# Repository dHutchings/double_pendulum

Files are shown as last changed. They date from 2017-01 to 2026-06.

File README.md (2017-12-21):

# double pendulum

A battery-powered low power double pendulum.  Useful for looking cool.  It's a good gift.

[Video of Final](https://youtu.be/Yj28coDq9EA)

[Video of Rev 3 Prototype](https://youtu.be/eYqc_CuFVBs)

[Video of Rev 2 Prototype](https://youtu.be/RyoI87ninAo)

[Video of Rev 1 Prototype](https://www.youtube.com/watch?v=9qNsIy8OKPE)

[Video of Proof of Concept](https://youtu.be/A4e-QBMb_Hc)

[Video of Back EMF Demo](https://youtu.be/CLvjtHWwjVc)

[BOM](https://docs.google.com/spreadsheets/d/1zQ9JefeK5bJ6EfoIBReY1vUxNtvPFnJwqca2jpHTiHs/edit#gid=1877369656)

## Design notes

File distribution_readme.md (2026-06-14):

## A List Showing the Distribution of Pendulums

#### Each Pendulum has a serial number, on a sticker, on the bottom of the base.

0. Douglas Hutchings  (Final prototype, brass is not polished)
1. Prof. Ronald Fearing (X)
2. Katherina Law (X) 
3. Prof. Oliver O'Reily (X)
4. Dr. George Anwar (X)
5. Jeremey Kramer (X)
6. Prof. Ruzena Bajcsy (X)
7. UC Berkeley MechE Machine Shop (X)
8. Dr. Eric Nelson (X)
9. Sold to Dr. Anwar (X)
10. Martin Kwitek (X)
11. Dr. Frank Ling (X)
12. Carl Page (X)
13. David Araujo ()

Intented:
14. Prof. Alice Agogino
15. Prof. Mark Mueller
16. Prof. Negar Mehr
17. UC Berkeley Hesse Hall Machine Shop
18. Dr. Deniz Dogruer
19. Dr. Alan Zhang
20. Katie Calvert
21. Kingston Chua
22. Ryan Ho.
23. Douglas Hutchings (rev E / D prototype)
24. Devin / Brian / Lee?  Tiffany / BG?

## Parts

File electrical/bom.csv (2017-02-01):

Name | Value | Package | Notes | Ref Number
C1 | 1000uF | CPOL-RADIAL-1000UF-25V | Capacitor Polarized
C2 | .1uF | 0603-CAP | Capacitor | CAPACITOR-GENERIC
C3 | 10uF | 0805 | Capacitor | CAPACITOR-GENERIC
C4 | .1uF | 0603-CAP | Capacitor | CAPACITOR-GENERIC
C5 | 10uF | 0805 | Capacitor | CAPACITOR-GENERIC
JP2 |  | 1X02 | 2-pin 0.1-inch header and MTA connector | BULK-STOCK
JP3 |  | 1X06 | PIN HEADER
Q1 | IRLIB9343PBF-ND | TO220 | P-Channel Enhancement MOSFET (HEXFET); -100V; -12A; 0,3Ohm
R1 | 10K | R0603 | RESISTOR, American symbol
R2 | 10K | R0603 | RESISTOR, American symbol
R3 | 10K | R0603 | RESISTOR, American symbol
R4 | 10K | R0603 | RESISTOR, American symbol
R5 | 10K | R0603 | RESISTOR, American symbol
R6 | 10K | R0603 | RESISTOR, American symbol
R7 | 10K | R0603 | RESISTOR, American symbol
R8 | 115k | R0603 | RESISTOR, American symbol
R9 | 10K | R0603 | RESISTOR, American symbol
S1 |  | TACTILE-PTH | Momentary Switch | pth_pushbutton
S2 |  | TACTILE-PTH | Momentary Switch | pth_pushbutton
S3 |  | TACTILE-PTH | Momentary Switch | pth_pushbutton
S4 |  | TACTILE-PTH | Momentary Switch | pth_pushbutton
ST1 | 2PIN_SCREW | 2PIN_SCREW | 2 Pin Screw Terminal
ST2 | 2PIN_SCREW | 2PIN_SCREW | 2 Pin Screw Terminal
S_PWR | SPDT_TOGGLE_SWITCH | E-SWITCH-SPDT | Toggle Switch SPDT Panel Mount
U1 | POLOLU_D24V22F5 | POLOLU_D24V22F5
U2 | TPS3710 | SOT6 | TI Low Voltage monitoring chip.
U3 | MCP4725 | SOT23-6 | Microchip 12-bit I2C DAC, SOT23-6
U4 | MCP4725 | SOT23-6 | Microchip 12-bit I2C DAC, SOT23-6
U5 | MCP6002 | DIL08 | Single Op Amp 2.7V to 6.0V Single Supply CMOS
UC1 | ARDUINO_PRO_MICRO | ARDUINO_PRO_MICRO | Arduino Pro Micro
USB1 | USB-OTGMICRO-AB | USB-MICRO-AB | USB Connector | USB

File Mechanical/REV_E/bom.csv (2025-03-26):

ITEM NO. | PART NUMBER | DESCRIPTION | QTY.
1 | 90633A005 |  | 6
2 | 92949A112 |  | 4
3 | Plate |  | 1
4 | 9541K8 |  | 4
5 | Base |  | 1
6 | Pillar |  | 1
7 | FR144-ZZ |  | 4
8 | 6433 |  | 1
9 | TATP-683-13 |  | 1
10 | RC22 |  | 1
11 | 94035A138 |  | 1
12 | bearing_spacer_ 99040A316 |  | 4
13 | 93286A005 |  | 11
14 | 92210A112 |  | 3
15 | Mass_blank |  | 1
16 | bottom_link |  | 1
17 | PCB_rev_a |  | 1
18 | bearing_offset |  | 1
19 | 94035A517 |  | 1
20 | 91780A167 |  | 2
21 | 93286A005 |  | 6
22 | 1155_battery_holder |  | 1
23 | 92141A009 |  | 2
24 | 93135A353 |  | 2
25 | 92949A113 |  | 2
26 | 92949A197 |  | 3
27 | top_link |  | 1

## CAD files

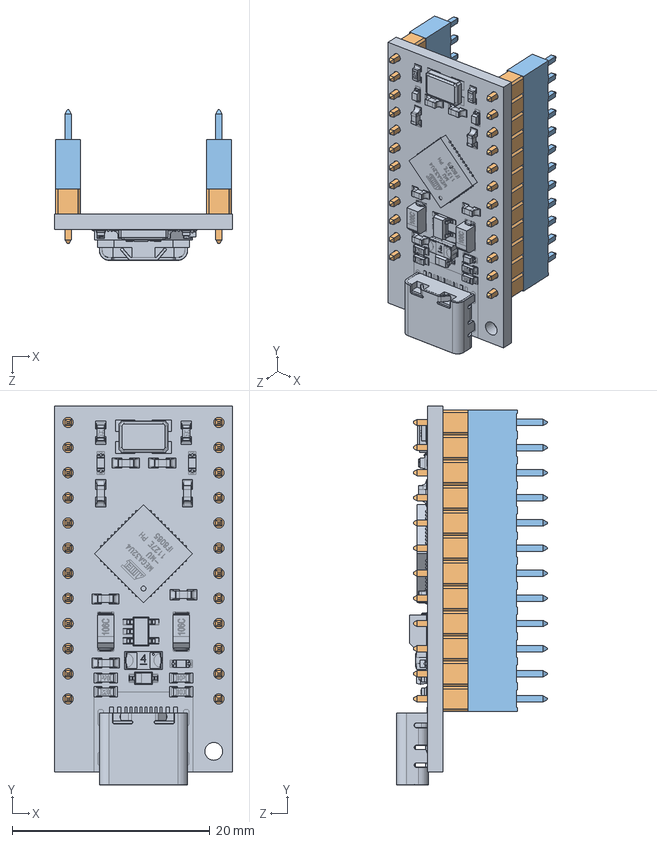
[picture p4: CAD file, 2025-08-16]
Mechanical/REV_E/pcb_parts/apm_usbc_removable.SLDASM
18.0 x 38.3 x 15.2 mm
ProMicroUSBC_Corrected
12pin_male_short x 2
12pin_female_short x 2

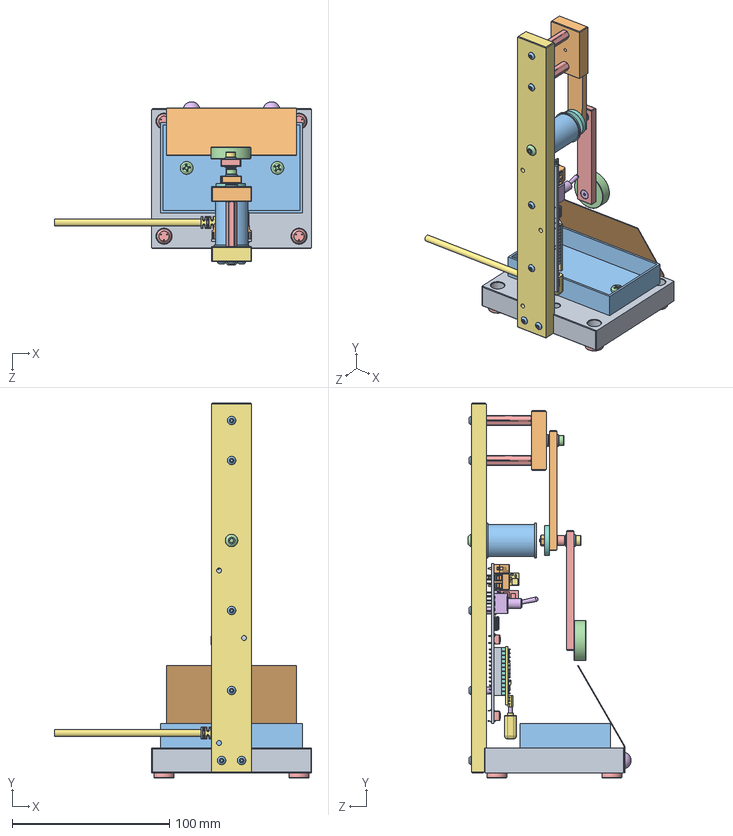
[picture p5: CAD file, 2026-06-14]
Mechanical/REV_E/Assem1.SLDASM
163.3 x 238.1 x 103.8 mm
Base
Plate
1155_battery_holder
8_32_500_nylon_93135A353 x 2
9309K62_Tight-Grip Push-In Bumpers x 4
90081A291_Zinc-Plated Steel Screw Nails x 2
Pillar
custom_spool x 2
Part4^electromagnet
8_32-750_stainless_92949A197
d45v1e1fx-step-down-voltage-regulators.step.step
Right angle pin header_03.step.step
step-up-voltage-regulator-u3v16fx.step.step
Right angle pin header_03.step (1).step
Board.step
2PIN_SCREW.step x 2
MCP6232.step x 2
0.033uF.step x 2
TACTILE-PTH.step x 4
SPDT_TOGGLE_SWITCH.step
STAND-OFFKEYSTONE_SMT_STANDOFF.step x 2
USB-C-16P-2LAYER-PADS.step
ICM7555.step
4.7uF.step x 2
600mA_40V.step
DMP3098.step
250mA_100V_350mV.step
220k.step x 3
220.step
CD40109B.step
LTC1661MSOP8.step
bearing_offset
4_40-625-Stainless-92949A811 x 6
4_40-625-countersunk-stainless-92210a112 x 2
4_40-1125-HEX Standoff_91780A629_Hex x 2
4_40_1-8_90176A102_Nylon Unthreaded Spacers x 2
ProMicroUSBC_Corrected
12pin_male_short x 2
12pin_female_short x 2
top_link
FR144-ZZ x 4
Mass_blank
bottom_link
92805A108_Stainless Steel Thread-Locking Hex Drive Flat Head Screws
4_40-3-4-94035A138
RC22
bearing_spacer_ 99040A316 x 4
4_40_THIN_LOCKNUT_90633A005
4_40-Washer_AL_93286A005
4_40-5-16_94035A517_new
1_8_3_16_92510A421_Aluminum Unthreaded Spacer-mod
Male USB C.step
USB C cord.step

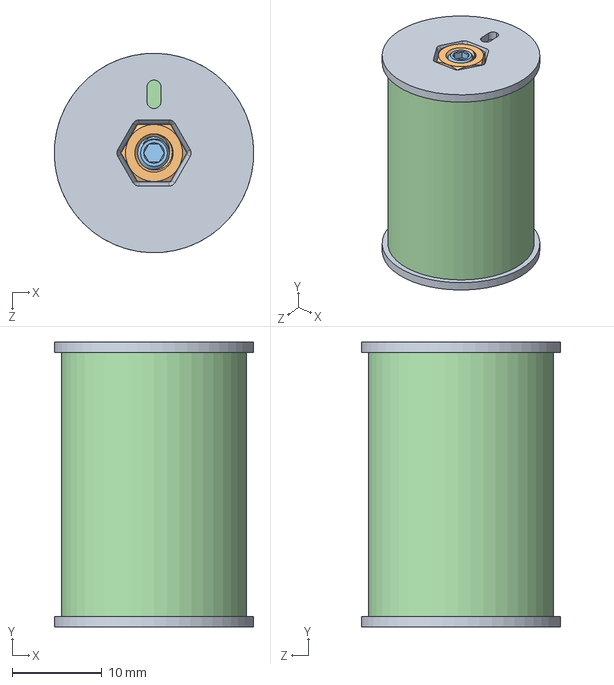
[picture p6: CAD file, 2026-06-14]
Mechanical/REV_E/electromagnet.SLDASM
22.2 x 31.8 x 22.2 mm
custom_spool x 2

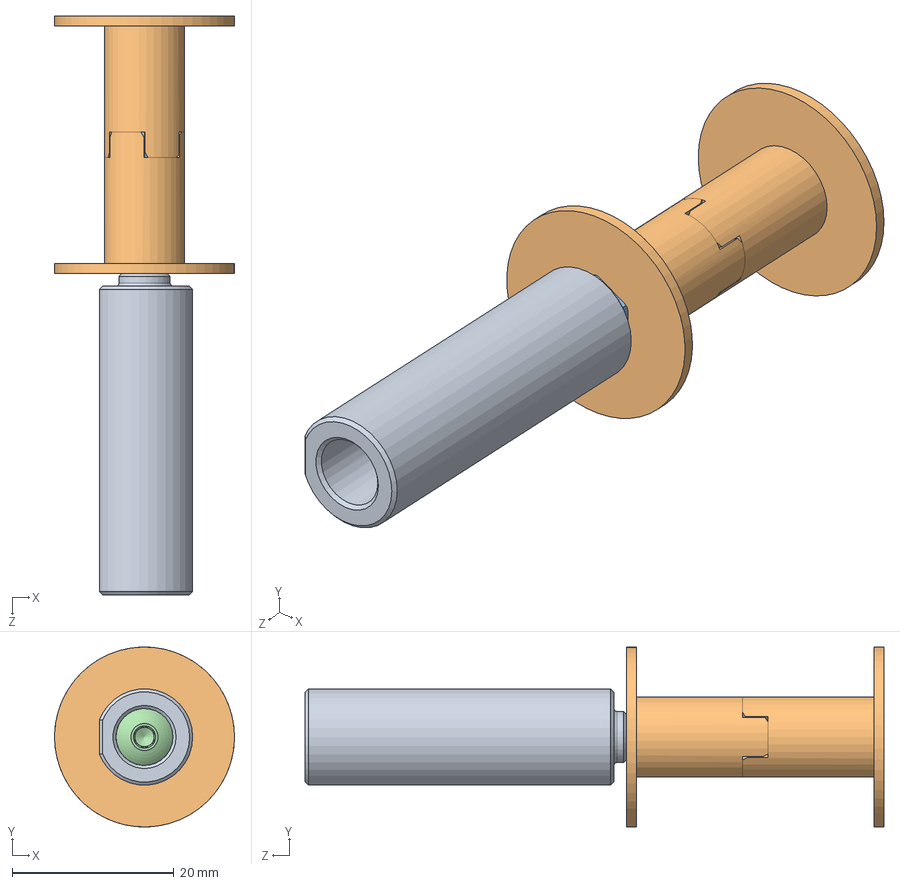
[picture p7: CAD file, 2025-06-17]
Mechanical/REV_E/tools/mandrel_assy.SLDASM
22.2 x 22.2 x 71.4 mm
winding_mandrel_machined
custom_spool x 2
91920A201_Female Threaded Hex Standoff
92949A197_18-8 Stainless Steel Button Head Hex Drive Screw

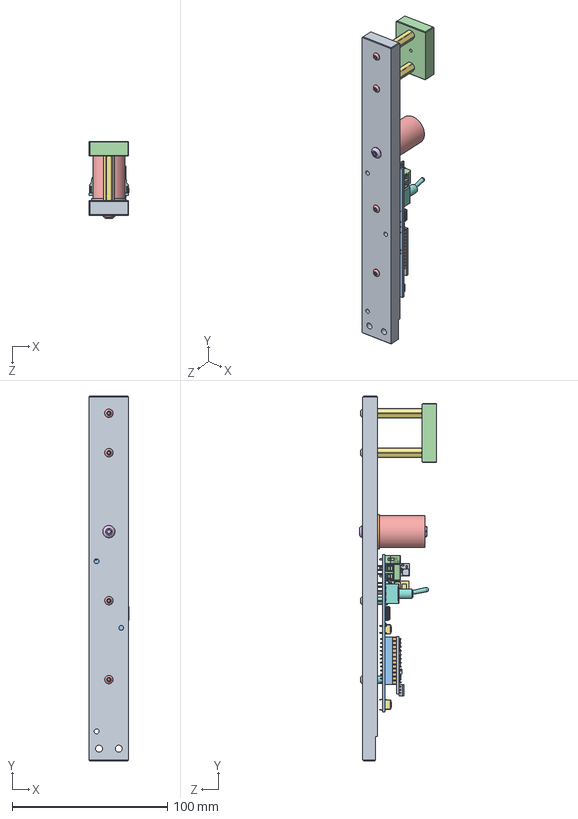
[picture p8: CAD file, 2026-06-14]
Mechanical/REV_E/Pillar_assy.sldasm
25.5 x 235.0 x 49.8 mm
Pillar
custom_spool
8_32-750_stainless_92949A197
d45v1e1fx-step-down-voltage-regulators.step.step
Right angle pin header_03.step.step
step-up-voltage-regulator-u3v16fx.step.step
Right angle pin header_03.step (1).step
Board.step
2PIN_SCREW.step x 2
MCP6232.step x 2
0.033uF.step x 2
TACTILE-PTH.step x 4
SPDT_TOGGLE_SWITCH.step
STAND-OFFKEYSTONE_SMT_STANDOFF.step x 2
USB-C-16P-2LAYER-PADS.step
ICM7555.step
4.7uF.step x 2
600mA_40V.step
DMP3098.step
250mA_100V_350mV.step
220k.step x 3
220.step
CD40109B.step
LTC1661MSOP8.step
bearing_offset
4_40-625-Stainless-92949A811 x 4
4_40-625-countersunk-stainless-92210a112 x 2
4_40-1125-HEX Standoff_91780A629_Hex x 2
4_40_1-8_90176A102_Nylon Unthreaded Spacers x 2
ProMicroUSBC_Corrected
12pin_male_short x 2
12pin_female_short x 2

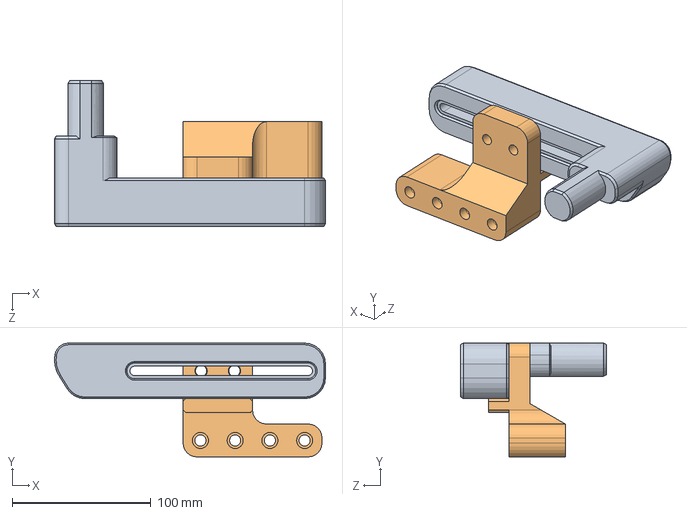
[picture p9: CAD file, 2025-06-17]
Mechanical/REV_E/tools/ShearStopAssy.SLDASM
195.0 x 81.9 x 105.0 mm
Press_brake_stop
ShearLowerArm

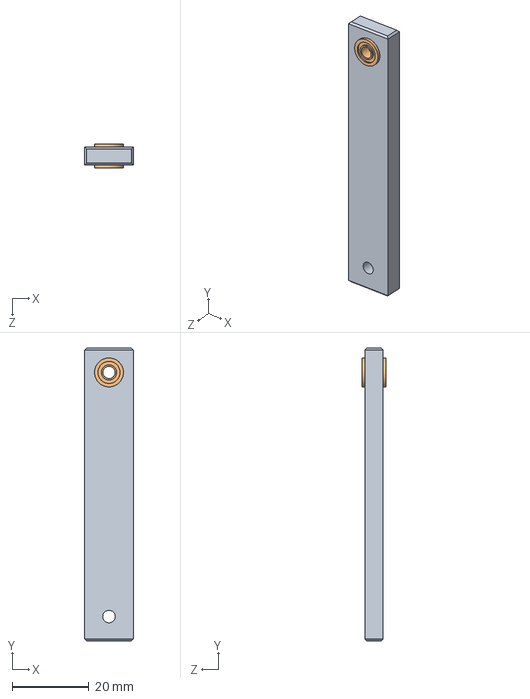
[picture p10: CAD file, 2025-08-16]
Mechanical/REV_E/top_link_assy.sldasm
12.7 x 76.2 x 6.34 mm
top_link
FR144-ZZ x 2

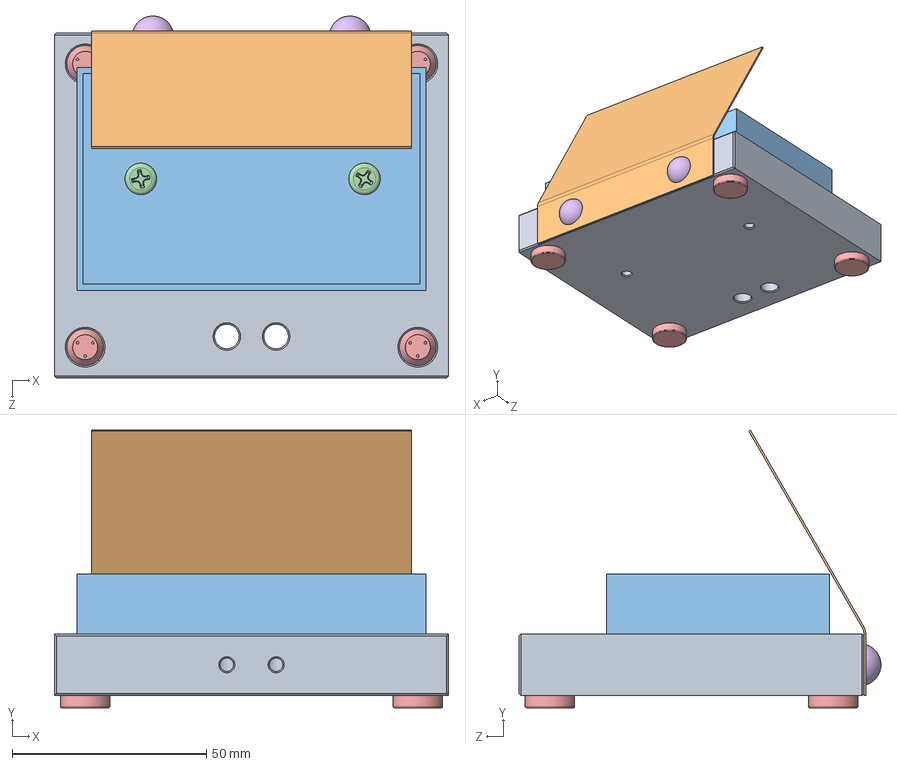
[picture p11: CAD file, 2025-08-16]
Mechanical/REV_E/Base_assy.sldasm
101.6 x 71.6 x 93.3 mm
Base
Plate
1155_battery_holder
8_32_500_nylon_93135A353 x 2
9309K62_Tight-Grip Push-In Bumpers x 4
90081A291_Zinc-Plated Steel Screw Nails x 2

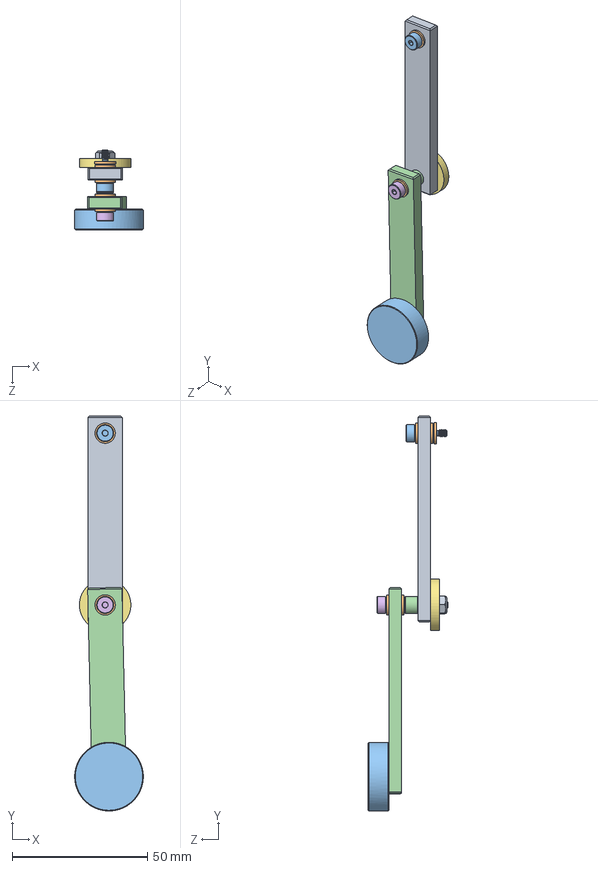
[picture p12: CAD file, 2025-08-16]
Mechanical/REV_E/pendulum.SLDASM
25.4 x 146.0 x 29.4 mm
top_link
FR144-ZZ x 4
Mass_blank
bottom_link
92805A108_Stainless Steel Thread-Locking Hex Drive Flat Head Screws
4_40-3-4-94035A138
RC22
bearing_spacer_ 99040A316 x 4
4_40_THIN_LOCKNUT_90633A005
4_40-Washer_AL_93286A005
4_40-5-16_94035A517_new
1_8_3_16_92510A421_Aluminum Unthreaded Spacer-mod

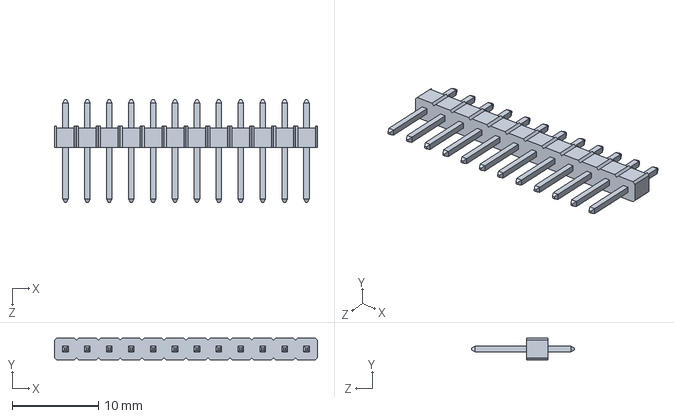
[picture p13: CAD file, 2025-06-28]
Mechanical/REV_E/pcb_parts/12pin_male.SLDASM
30.5 x 2.54 x 11.9 mm

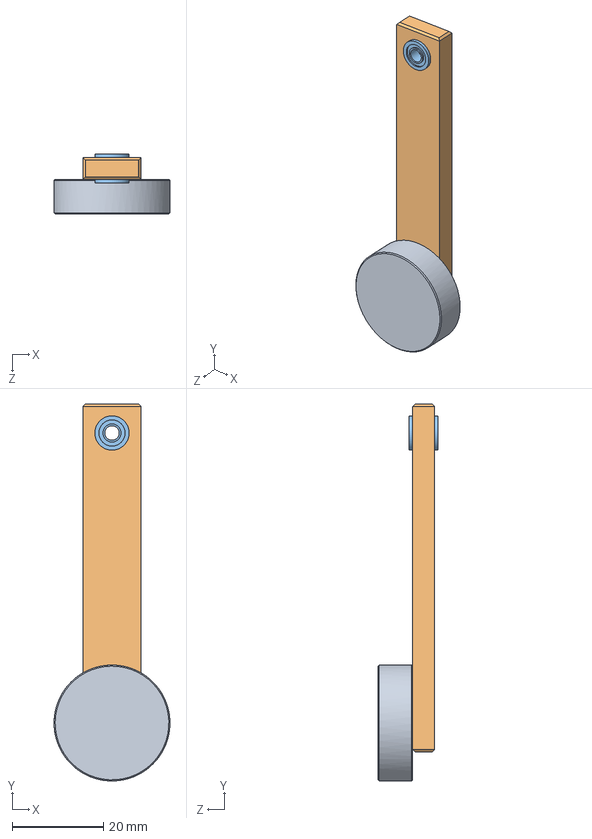
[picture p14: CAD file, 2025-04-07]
Mechanical/REV_E/bottom_link_assy.sldasm
25.4 x 82.5 x 13.2 mm
Mass_blank
bottom_link
FR144-ZZ x 2
92805A108_Stainless Steel Thread-Locking Hex Drive Flat Head Screws

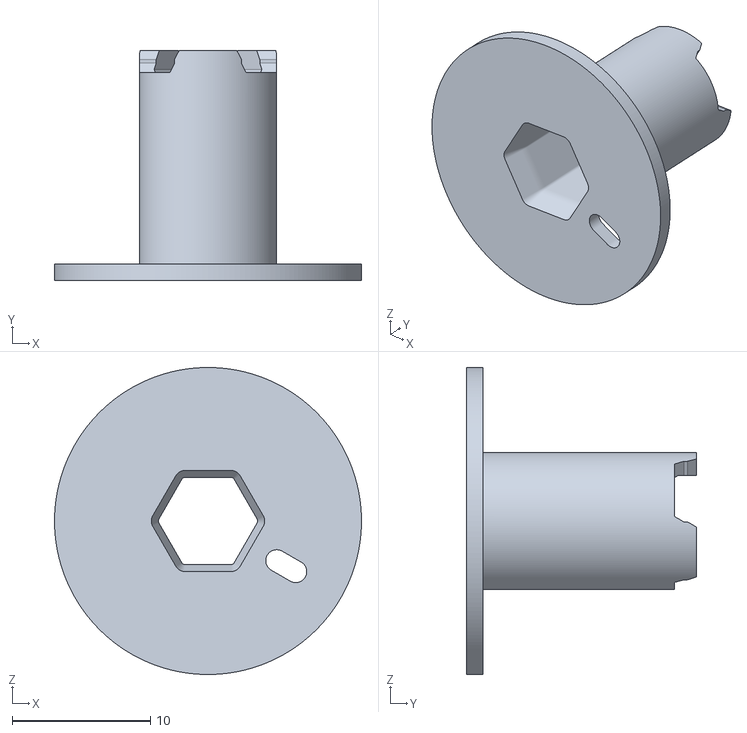
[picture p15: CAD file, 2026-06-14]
Mechanical/REV_E/printables/custom_spool_xometry_pressfit.STL
22.2 x 16.7 x 22.2

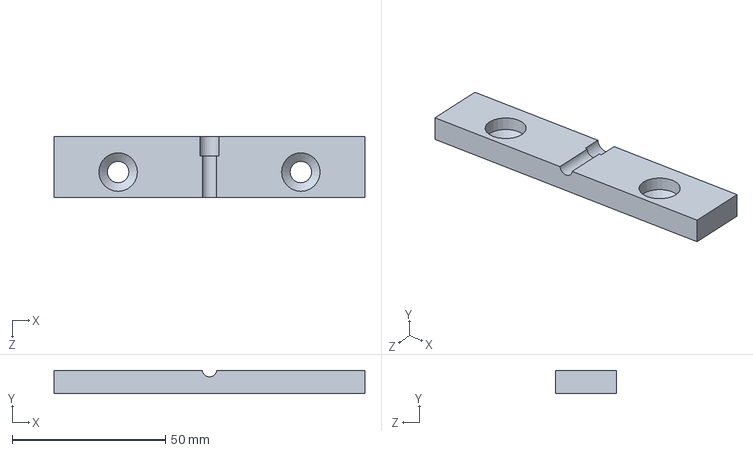
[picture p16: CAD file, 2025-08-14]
Mechanical/REV_E/tools/clamp.SLDPRT
101.6 x 7.62 x 19.8 mm

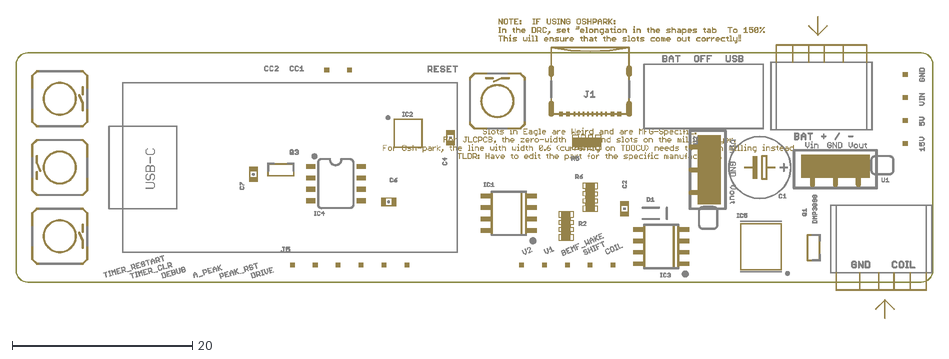
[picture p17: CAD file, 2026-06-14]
Mechanical/REV_E/controller_revD5.dxf
101.6 x 33.5

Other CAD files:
Mechanical/REV_E/controller_d5_san.DXF
Mechanical/REV_E/pcb_parts/Right angle pin header_03.STEP
Mechanical/REV_E/printables/custom_spool_xometry_clearance.STL
Mechanical/REV_E/tools/winding_mandrel_machined.SLDPRT
Mechanical/REV_C/4-40-75-92949A113_.SLDPRT
Mechanical/REV_C/4-40-750-Nylon_93135A278.SLDPRT
Mechanical/REV_C/4-40_15-32_5-32_94035A134.SLDPRT
Mechanical/REV_C/4-40_7-16_5-32_94035A521.SLDPRT
Mechanical/REV_C/4_40-125_spacer_nylon_94639A199.SLDPRT
Mechanical/REV_C/4_40-50-91255A110.SLDPRT
Mechanical/REV_C/4_40-50-92949A110.SLDPRT
Mechanical/REV_C/4_40-562-Stainless-92949A112.SLDPRT
Mechanical/REV_C/4_40-625-countersunk-91253A112.SLDPRT
Mechanical/REV_C/4_40-75-91255A113.SLDPRT
Mechanical/REV_C/4_40-Washer_AL_93286A005.SLDPRT
Mechanical/REV_C/4_40_1750-HEX STANDOFF91780A038.SLDPRT
Mechanical/REV_C/8_32-625-97763A333.SLDPRT
Mechanical/REV_C/8_32-750-91255A197-new.SLDPRT
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

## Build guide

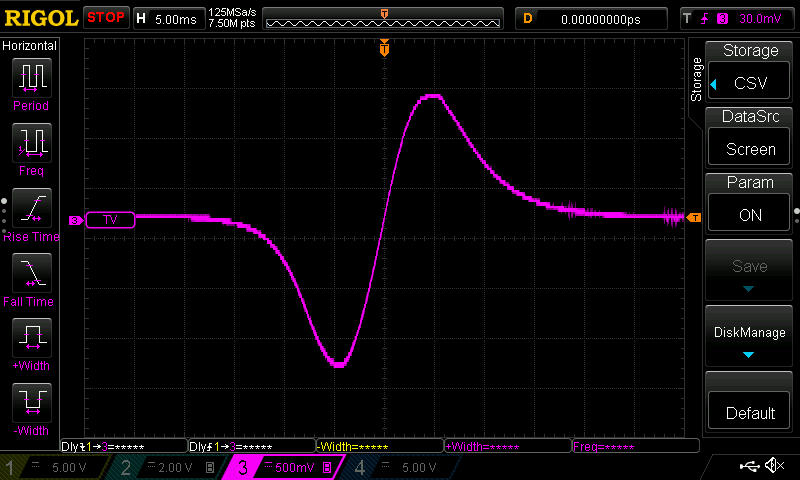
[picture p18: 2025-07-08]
electrical/back_emf/DS1Z_QuickPrint5_ragged.jpg

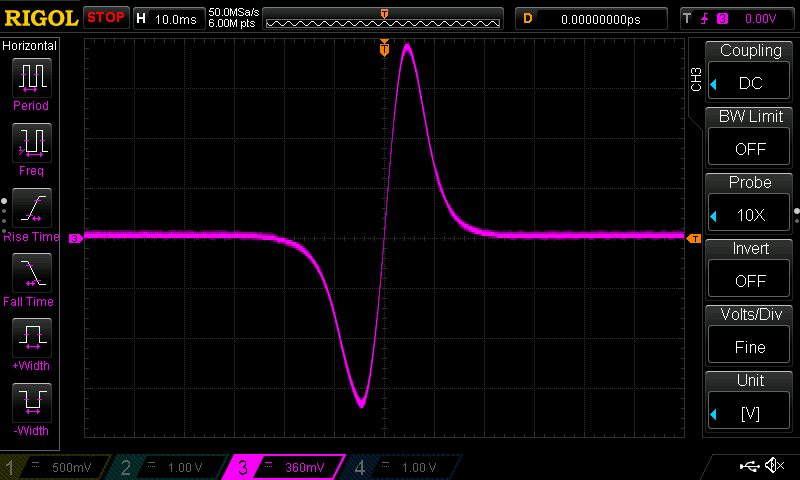
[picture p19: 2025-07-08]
electrical/back_emf/DS1Z_QuickPrint1_clean.png

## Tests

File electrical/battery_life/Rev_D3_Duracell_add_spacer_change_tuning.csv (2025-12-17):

FLUKE 289 | V1.16 | 40810170 Douglas Hutchings
To display full timestamps use Format Cells ‘m/d/y hh:mm:ss.0'
Start Time | Stop Time | Elapsed Time | Interval | Total readings | Intervals | Input Events | Session Name
12/14/2025 6:20:07 PM | 12/16/2025 11:44:42 AM | 41:24:35 | 0:01:00 | 11096 | 2485 | 8786 | Motor 11
Max Time | Max | Average | Min | Min Time | Scaling
12/14/2025 6:20:07 PM | 10.130 V DC | 6.737 V DC | 1.3092 V DC | 12/16/2025 12:12:04 AM | (none)
Reading | Sample | Start Time | Duration | Max Time | Max | Average | Min Time | Min | Description | Stop Time
1 | 10.130 V DC | 12/14/2025 18:20:07.3 | 0:00:03.2 | 12/14/2025 18:20:07.3 | 10.130 V DC | 10.108 V DC | 12/14/2025 18:20:10.1 | 10.033 V DC | Stable | 12/14/2025 18:20:10.5
2 | 9.406 V DC | 12/14/2025 18:20:10.5 | 0:00:03.2 | 12/14/2025 18:20:11.2 | 9.943 V DC | 9.084 V DC | 12/14/2025 18:20:13.1 | 8.402 V DC | Unstable | 12/14/2025 18:20:13.7
3 | 9.884 V DC | 12/14/2025 18:20:13.7 | 0:00:01.9 | 12/14/2025 18:20:15.6 | 9.987 V DC | 9.948 V DC | 12/14/2025 18:20:13.7 | 9.884 V DC | Stable | 12/14/2025 18:20:15.7
4 | 9.990 V DC | 12/14/2025 18:20:15.7 | 0:00:04.6 | 12/14/2025 18:20:16.1 | 10.000 V DC | 9.266 V DC | 12/14/2025 18:20:19.1 | 8.384 V DC | Unstable | 12/14/2025 18:20:20.3
5 | 9.859 V DC | 12/14/2025 18:20:20.3 | 0:00:06.8 | 12/14/2025 18:20:23.7 | 9.960 V DC | 9.908 V DC | 12/14/2025 18:20:20.5 | 9.799 V DC | Stable | 12/14/2025 18:20:27.1
6 | 9.977 V DC | 12/14/2025 18:20:27.1 | 0:00:00.1 | 12/14/2025 18:20:27.1 | 9.977 V DC | 9.977 V DC | 12/14/2025 18:20:27.1 | 9.977 V DC | Unstable | 12/14/2025 18:20:27.2
7 | 9.868 V DC | 12/14/2025 18:20:27.2 | 0:00:02.8 | 12/14/2025 18:20:29.8 | 10.005 V DC | 9.980 V DC | 12/14/2025 18:20:27.2 | 9.868 V DC | Stable | 12/14/2025 18:20:30.0
8 | 10.006 V DC | 12/14/2025 18:20:30.0 | 0:00:03.1 | 12/14/2025 18:20:32.5 | 10.018 V DC | 9.995 V DC | 12/14/2025 18:20:32.9 | 9.957 V DC | Stable | 12/14/2025 18:20:33.2
9 | 9.876 V DC | 12/14/2025 18:20:33.2 | 0:00:00.3 | 12/14/2025 18:20:33.4 | 9.993 V DC | 9.939 V DC | 12/14/2025 18:20:33.2 | 9.876 V DC | Unstable | 12/14/2025 18:20:33.5
10 | 10.012 V DC | 12/14/2025 18:20:33.5 | 0:00:33.3 | 12/14/2025 18:21:04.4 | 10.055 V DC | 10.024 V DC | 12/14/2025 18:21:00.6 | 9.923 V DC | Interval | 12/14/2025 18:21:06.8
11 | 9.996 V DC | 12/14/2025 18:21:06.8 | 0:00:37.1 | 12/14/2025 18:21:42.3 | 10.066 V DC | 10.044 V DC | 12/14/2025 18:21:21.8 | 9.934 V DC | Stable | 12/14/2025 18:21:43.9
12 | 9.917 V DC | 12/14/2025 18:21:43.9 | 0:00:00.1 | 12/14/2025 18:21:43.9 | 9.917 V DC | 9.917 V DC | 12/14/2025 18:21:43.9 | 9.917 V DC | Unstable | 12/14/2025 18:21:44.0
13 | 10.036 V DC | 12/14/2025 18:21:44.0 | 0:00:14.8 | 12/14/2025 18:21:52.2 | 10.063 V DC | 10.041 V DC | 12/14/2025 18:21:46.3 | 9.965 V DC | Stable | 12/14/2025 18:21:58.8
14 | 9.911 V DC | 12/14/2025 18:21:58.8 | 0:00:00.1 | 12/14/2025 18:21:58.8 | 9.911 V DC | 9.911 V DC | 12/14/2025 18:21:58.8 | 9.911 V DC | Unstable | 12/14/2025 18:21:58.9
15 | 10.039 V DC | 12/14/2025 18:21:58.9 | 0:00:07.8 | 12/14/2025 18:22:01.4 | 10.063 V DC | 10.045 V DC | 12/14/2025 18:22:00.7 | 9.988 V DC | Interval | 12/14/2025 18:22:06.7
16 | 10.064 V DC | 12/14/2025 18:22:06.7 | 0:00:17.2 | 12/14/2025 18:22:17.7 | 10.065 V DC | 10.043 V DC | 12/14/2025 18:22:19.6 | 9.942 V DC | Stable | 12/14/2025 18:22:23.9
17 | 9.870 V DC | 12/14/2025 18:22:23.9 | 0:00:00.1 | 12/14/2025 18:22:23.9 | 9.870 V DC | 9.870 V DC | 12/14/2025 18:22:23.9 | 9.870 V DC | Unstable | 12/14/2025 18:22:24.0
18 | 10.025 V DC | 12/14/2025 18:22:24.0 | 0:00:03.9 | 12/14/2025 18:22:27.9 | 10.063 V DC | 10.042 V DC | 12/14/2025 18:22:26.8 | 9.969 V DC | Stable | 12/14/2025 18:22:28.0
19 | 9.927 V DC | 12/14/2025 18:22:28.0 | 0:00:00.2 | 12/14/2025 18:22:28.1 | 9.961 V DC | 9.944 V DC | 12/14/2025 18:22:28.0 | 9.927 V DC | Unstable | 12/14/2025 18:22:28.2
20 | 10.046 V DC | 12/14/2025 18:22:28.2 | 0:00:25.1 | 12/14/2025 18:22:49.5 | 10.065 V DC | 10.043 V DC | 12/14/2025 18:22:35.2 | 9.957 V DC | Stable | 12/14/2025 18:22:53.3
21 | 9.938 V DC | 12/14/2025 18:22:53.3 | 0:00:00.1 | 12/14/2025 18:22:53.3 | 9.938 V DC | 9.938 V DC | 12/14/2025 18:22:53.3 | 9.938 V DC | Unstable | 12/14/2025 18:22:53.4
22 | 10.047 V DC | 12/14/2025 18:22:53.4 | 0:00:01.1 | 12/14/2025 18:22:54.4 | 10.062 V DC | 10.049 V DC | 12/14/2025 18:22:53.6 | 10.021 V DC | Stable | 12/14/2025 18:22:54.5
23 | 9.938 V DC | 12/14/2025 18:22:54.5 | 0:00:00.4 | 12/14/2025 18:22:54.8 | 10.040 V DC | 9.972 V DC | 12/14/2025 18:22:54.5 | 9.938 V DC | Unstable | 12/14/2025 18:22:54.9
24 | 10.056 V DC | 12/14/2025 18:22:54.9 | 0:00:11.9 | 12/14/2025 18:23:04.3 | 10.063 V DC | 10.039 V DC | 12/14/2025 18:22:57.9 | 9.946 V DC | Interval | 12/14/2025 18:23:06.8
25 | 10.061 V DC | 12/14/2025 18:23:06.8 | 0:00:07.3 | 12/14/2025 18:23:11.3 | 10.063 V DC | 10.043 V DC | 12/14/2025 18:23:06.9 | 9.981 V DC | Stable | 12/14/2025 18:23:14.1
26 | 9.904 V DC | 12/14/2025 18:23:14.1 | 0:00:00.1 | 12/14/2025 18:23:14.1 | 9.904 V DC | 9.904 V DC | 12/14/2025 18:23:14.1 | 9.904 V DC | Unstable | 12/14/2025 18:23:14.3
27 | 10.041 V DC | 12/14/2025 18:23:14.3 | 0:00:41.5 | 12/14/2025 18:23:23.8 | 10.063 V DC | 10.043 V DC | 12/14/2025 18:23:32.1 | 9.943 V DC | Stable | 12/14/2025 18:23:55.8
28 | 9.930 V DC | 12/14/2025 18:23:55.8 | 0:00:11.0 | 12/14/2025 18:23:59.7 | 10.061 V DC | 10.032 V DC | 12/14/2025 18:24:05.5 | 9.915 V DC | Interval | 12/14/2025 18:24:06.8
29 | 10.058 V DC | 12/14/2025 18:24:06.8 | 0:00:01.2 | 12/14/2025 18:24:06.8 | 10.058 V DC | 10.033 V DC | 12/14/2025 18:24:07.7 | 9.935 V DC | Unstable | 12/14/2025 18:24:08.0
30 | 10.055 V DC | 12/14/2025 18:24:08.0 | 0:00:58.8 | 12/14/2025 18:24:26.5 | 10.060 V DC | 10.037 V DC | 12/14/2025 18:24:32.0 | 9.925 V DC | Interval | 12/14/2025 18:25:06.7
31 | 10.058 V DC | 12/14/2025 18:25:06.7 | 0:00:02.7 | 12/14/2025 18:25:06.8 | 10.059 V DC | 10.045 V DC | 12/14/2025 18:25:08.4 | 9.986 V DC | Stable | 12/14/2025 18:25:09.4
32 | 9.939 V DC | 12/14/2025 18:25:09.4 | 0:00:57.3 | 12/14/2025 18:25:22.8 | 10.057 V DC | 10.033 V DC | 12/14/2025 18:25:15.5 | 9.889 V DC | Interval | 12/14/2025 18:26:06.8
33 | 10.052 V DC | 12/14/2025 18:26:06.8 | 0:00:12.7 | 12/14/2025 18:26:08.2 | 10.055 V DC | 10.032 V DC | 12/14/2025 18:26:10.2 | 9.953 V DC | Stable | 12/14/2025 18:26:19.5
34 | 9.934 V DC | 12/14/2025 18:26:19.5 | 0:00:00.1 | 12/14/2025 18:26:19.5 | 9.934 V DC | 9.934 V DC | 12/14/2025 18:26:19.5 | 9.934 V DC | Unstable | 12/14/2025 18:26:19.6
35 | 10.036 V DC | 12/14/2025 18:26:19.6 | 0:00:06.5 | 12/14/2025 18:26:23.1 | 10.052 V DC | 10.027 V DC | 12/14/2025 18:26:20.4 | 9.934 V DC | Stable | 12/14/2025 18:26:26.1
36 | 9.915 V DC | 12/14/2025 18:26:26.1 | 0:00:40.6 | 12/14/2025 18:26:29.2 | 10.051 V DC | 10.025 V DC | 12/14/2025 18:26:42.8 | 9.857 V DC | Interval | 12/14/2025 18:27:06.8
37 | 10.048 V DC | 12/14/2025 18:27:06.8 | 0:00:17.4 | 12/14/2025 18:27:07.6 | 10.049 V DC | 10.028 V DC | 12/14/2025 18:27:07.7 | 9.946 V DC | Stable | 12/14/2025 18:27:24.2
38 | 9.896 V DC | 12/14/2025 18:27:24.2 | 0:00:07.5 | 12/14/2025 18:27:26.5 | 10.044 V DC | 10.011 V DC | 12/14/2025 18:27:28.2 | 9.894 V DC | Stable | 12/14/2025 18:27:31.7
39 | 10.045 V DC | 12/14/2025 18:27:31.7 | 0:00:23.9 | 12/14/2025 18:27:48.6 | 10.047 V DC | 10.022 V DC | 12/14/2025 18:27:34.8 | 9.922 V DC | Stable | 12/14/2025 18:27:55.7
40 | 9.877 V DC | 12/14/2025 18:27:55.7 | 0:00:00.1 | 12/14/2025 18:27:55.7 | 9.877 V DC | 9.877 V DC | 12/14/2025 18:27:55.7 | 9.877 V DC | Unstable | 12/14/2025 18:27:55.8
41 | 9.996 V DC | 12/14/2025 18:27:55.8 | 0:00:11.1 | 12/14/2025 18:28:04.0 | 10.041 V DC | 10.002 V DC | 12/14/2025 18:27:57.2 | 9.886 V DC | Interval | 12/14/2025 18:28:06.8
42 | 9.987 V DC | 12/14/2025 18:28:06.8 | 0:00:10.4 | 12/14/2025 18:28:12.6 | 10.042 V DC | 10.019 V DC | 12/14/2025 18:28:12.8 | 9.926 V DC | Stable | 12/14/2025 18:28:17.2
43 | 9.888 V DC | 12/14/2025 18:28:17.2 | 0:00:00.1 | 12/14/2025 18:28:17.2 | 9.888 V DC | 9.888 V DC | 12/14/2025 18:28:17.2 | 9.888 V DC | Unstable | 12/14/2025 18:28:17.3
44 | 10.017 V DC | 12/14/2025 18:28:17.3 | 0:00:13.7 | 12/14/2025 18:28:20.6 | 10.041 V DC | 10.021 V DC | 12/14/2025 18:28:27.9 | 9.942 V DC | Stable | 12/14/2025 18:28:31.0
45 | 9.924 V DC | 12/14/2025 18:28:31.0 | 0:00:35.8 | 12/14/2025 18:28:33.9 | 10.043 V DC | 10.017 V DC | 12/14/2025 18:28:57.4 | 9.880 V DC | Interval | 12/14/2025 18:29:06.8
46 | 10.036 V DC | 12/14/2025 18:29:06.8 | 0:00:02.9 | 12/14/2025 18:29:07.6 | 10.040 V DC | 10.024 V DC | 12/14/2025 18:29:08.9 | 9.961 V DC | Stable | 12/14/2025 18:29:09.7
47 | 9.915 V DC | 12/14/2025 18:29:09.7 | 0:00:00.1 | 12/14/2025 18:29:09.7 | 9.915 V DC | 9.915 V DC | 12/14/2025 18:29:09.7 | 9.915 V DC | Unstable | 12/14/2025 18:29:09.8
48 | 10.020 V DC | 12/14/2025 18:29:09.8 | 0:00:15.5 | 12/14/2025 18:29:14.4 | 10.040 V DC | 10.014 V DC | 12/14/2025 18:29:15.1 | 9.929 V DC | Stable | 12/14/2025 18:29:25.3
49 | 9.925 V DC | 12/14/2025 18:29:25.3 | 0:00:41.4 | 12/14/2025 18:30:00.3 | 10.038 V DC | 10.014 V DC | 12/14/2025 18:29:25.6 | 9.880 V DC | Interval | 12/14/2025 18:30:06.7
50 | 10.029 V DC | 12/14/2025 18:30:06.7 | 0:00:09.1 | 12/14/2025 18:30:10.5 | 10.037 V DC | 10.017 V DC | 12/14/2025 18:30:07.0 | 9.939 V DC | Stable | 12/14/2025 18:30:15.8
51 | 9.929 V DC | 12/14/2025 18:30:15.8 | 0:00:51.0 | 12/14/2025 18:30:21.6 | 10.036 V DC | 10.012 V DC | 12/14/2025 18:30:56.8 | 9.881 V DC | Interval | 12/14/2025 18:31:06.8
52 | 10.028 V DC | 12/14/2025 18:31:06.8 | 0:00:26.3 | 12/14/2025 18:31:16.7 | 10.034 V DC | 10.010 V DC | 12/14/2025 18:31:29.5 | 9.919 V DC | Stable | 12/14/2025 18:31:33.1
53 | 9.897 V DC | 12/14/2025 18:31:33.1 | 0:00:33.7 | 12/14/2025 18:31:46.3 | 10.029 V DC | 10.000 V DC | 12/14/2025 18:31:33.1 | 9.897 V DC | Interval | 12/14/2025 18:32:06.8
54 | 10.025 V DC | 12/14/2025 18:32:06.8 | 0:00:16.2 | 12/14/2025 18:32:11.7 | 10.028 V DC | 10.004 V DC | 12/14/2025 18:32:22.8 | 9.931 V DC | Stable | 12/14/2025 18:32:23.0
55 | 9.916 V DC | 12/14/2025 18:32:23.0 | 0:00:44.1 | 12/14/2025 18:32:30.5 | 10.027 V DC | 9.998 V DC | 12/14/2025 18:32:32.8 | 9.871 V DC | Interval | 12/14/2025 18:33:07.0
56 | 10.021 V DC | 12/14/2025 18:33:07.0 | 0:00:31.6 | 12/14/2025 18:33:31.6 | 10.023 V DC | 9.999 V DC | 12/14/2025 18:33:12.3 | 9.909 V DC | Stable | 12/14/2025 18:33:38.6
57 | 9.869 V DC | 12/14/2025 18:33:38.6 | 0:00:00.1 | 12/14/2025 18:33:38.6 | 9.869 V DC | 9.869 V DC | 12/14/2025 18:33:38.6 | 9.869 V DC | Unstable | 12/14/2025 18:33:38.7
58 | 9.995 V DC | 12/14/2025 18:33:38.7 | 0:00:16.9 | 12/14/2025 18:33:44.8 | 10.021 V DC | 10.002 V DC | 12/14/2025 18:33:51.5 | 9.934 V DC | Stable | 12/14/2025 18:33:55.6
59 | 9.841 V DC | 12/14/2025 18:33:55.6 | 0:00:00.1 | 12/14/2025 18:33:55.6 | 9.841 V DC | 9.841 V DC | 12/14/2025 18:33:55.6 | 9.841 V DC | Unstable | 12/14/2025 18:33:55.7
60 | 9.989 V DC | 12/14/2025 18:33:55.7 | 0:00:11.1 | 12/14/2025 18:34:01.4 | 10.020 V DC | 9.999 V DC | 12/14/2025 18:33:55.9 | 9.926 V DC | Interval | 12/14/2025 18:34:06.8
61 | 10.005 V DC | 12/14/2025 18:34:06.8 | 0:00:06.1 | 12/14/2025 18:34:08.4 | 10.021 V DC | 9.998 V DC | 12/14/2025 18:34:12.3 | 9.924 V DC | Stable | 12/14/2025 18:34:12.9
62 | 9.886 V DC | 12/14/2025 18:34:12.9 | 0:00:00.1 | 12/14/2025 18:34:12.9 | 9.886 V DC | 9.886 V DC | 12/14/2025 18:34:12.9 | 9.886 V DC | Unstable | 12/14/2025 18:34:13.0
63 | 9.996 V DC | 12/14/2025 18:34:13.0 | 0:00:25.5 | 12/14/2025 18:34:24.4 | 10.020 V DC | 9.998 V DC | 12/14/2025 18:34:30.4 | 9.909 V DC | Stable | 12/14/2025 18:34:38.5
64 | 9.893 V DC | 12/14/2025 18:34:38.5 | 0:00:28.3 | 12/14/2025 18:34:45.3 | 10.019 V DC | 9.996 V DC | 12/14/2025 18:34:38.5 | 9.893 V DC | Interval | 12/14/2025 18:35:06.7
65 | 10.013 V DC | 12/14/2025 18:35:06.7 | 0:00:06.7 | 12/14/2025 18:35:09.1 | 10.017 V DC | 9.999 V DC | 12/14/2025 18:35:09.2 | 9.938 V DC | Stable | 12/14/2025 18:35:13.5
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

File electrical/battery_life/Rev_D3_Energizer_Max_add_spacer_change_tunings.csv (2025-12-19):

FLUKE 289 | V1.16 | 40810170 Douglas Hutchings
To display full timestamps use Format Cells ‘m/d/y hh:mm:ss.0'
Start Time | Stop Time | Elapsed Time | Interval | Total readings | Intervals | Input Events | Session Name
12/16/2025 12:10:30 PM | 12/17/2025 1:19:52 PM | 25:09:23 | 0:01:00 | 10121 | 1510 | 8783 | Motor 12
Max Time | Max | Average | Min | Min Time | Scaling
12/16/2025 12:10:30 PM | 9.695 V DC | 7.577 V DC | 1.336 V DC | 12/17/2025 9:58:43 AM | (none)
Reading | Sample | Start Time | Duration | Max Time | Max | Average | Min Time | Min | Description | Stop Time
1 | 9.695 V DC | 12/16/2025 12:10:29.9 | 0:00:05.3 | 12/16/2025 12:10:29.9 | 9.695 V DC | 8.931 V DC | 12/16/2025 12:10:31.8 | 7.747 V DC | Unstable | 12/16/2025 12:10:35.2
2 | 9.512 V DC | 12/16/2025 12:10:35.2 | 0:00:05.4 | 12/16/2025 12:10:40.5 | 9.612 V DC | 9.564 V DC | 12/16/2025 12:10:35.6 | 9.476 V DC | Stable | 12/16/2025 12:10:40.6
3 | 9.614 V DC | 12/16/2025 12:10:40.6 | 0:00:03.4 | 12/16/2025 12:10:43.9 | 9.628 V DC | 9.605 V DC | 12/16/2025 12:10:41.9 | 9.535 V DC | Stable | 12/16/2025 12:10:44.0
4 | 9.480 V DC | 12/16/2025 12:10:44.0 | 0:00:00.4 | 12/16/2025 12:10:44.3 | 9.613 V DC | 9.555 V DC | 12/16/2025 12:10:44.0 | 9.480 V DC | Unstable | 12/16/2025 12:10:44.4
5 | 9.625 V DC | 12/16/2025 12:10:44.4 | 0:00:44.8 | 12/16/2025 12:11:29.0 | 9.657 V DC | 9.628 V DC | 12/16/2025 12:11:16.9 | 9.507 V DC | Interval | 12/16/2025 12:11:29.2
6 | 9.628 V DC | 12/16/2025 12:11:29.2 | 0:00:18.7 | 12/16/2025 12:11:47.2 | 9.660 V DC | 9.637 V DC | 12/16/2025 12:11:42.9 | 9.548 V DC | Stable | 12/16/2025 12:11:47.9
7 | 8.747 V DC | 12/16/2025 12:11:47.9 | 0:00:03.4 | 12/16/2025 12:11:48.5 | 9.499 V DC | 8.619 V DC | 12/16/2025 12:11:50.5 | 7.804 V DC | Unstable | 12/16/2025 12:11:51.4
8 | 9.480 V DC | 12/16/2025 12:11:51.4 | 0:00:04.4 | 12/16/2025 12:11:55.1 | 9.572 V DC | 9.529 V DC | 12/16/2025 12:11:53.1 | 9.469 V DC | Stable | 12/16/2025 12:11:55.8
9 | 9.578 V DC | 12/16/2025 12:11:55.8 | 0:00:14.7 | 12/16/2025 12:12:09.9 | 9.624 V DC | 9.594 V DC | 12/16/2025 12:11:59.2 | 9.526 V DC | Stable | 12/16/2025 12:12:10.5
10 | 8.096 V DC | 12/16/2025 12:12:10.5 | 0:00:03.5 | 12/16/2025 12:12:11.1 | 9.492 V DC | 8.666 V DC | 12/16/2025 12:12:13.0 | 7.820 V DC | Unstable | 12/16/2025 12:12:14.0
11 | 9.464 V DC | 12/16/2025 12:12:14.0 | 0:00:07.0 | 12/16/2025 12:12:20.1 | 9.560 V DC | 9.513 V DC | 12/16/2025 12:12:14.2 | 9.414 V DC | Stable | 12/16/2025 12:12:21.0
12 | 9.564 V DC | 12/16/2025 12:12:21.0 | 0:00:08.2 | 12/16/2025 12:12:28.7 | 9.586 V DC | 9.558 V DC | 12/16/2025 12:12:24.1 | 9.467 V DC | Interval | 12/16/2025 12:12:29.2
13 | 9.534 V DC | 12/16/2025 12:12:29.2 | 0:01:00.1 | 12/16/2025 12:13:25.3 | 9.621 V DC | 9.591 V DC | 12/16/2025 12:12:33.0 | 9.488 V DC | Interval | 12/16/2025 12:13:29.2
14 | 9.575 V DC | 12/16/2025 12:13:29.2 | 0:00:44.2 | 12/16/2025 12:14:12.7 | 9.629 V DC | 9.607 V DC | 12/16/2025 12:13:33.0 | 9.505 V DC | Stable | 12/16/2025 12:14:13.4
15 | 9.468 V DC | 12/16/2025 12:14:13.4 | 0:00:03.8 | 12/16/2025 12:14:14.1 | 9.495 V DC | 8.812 V DC | 12/16/2025 12:14:15.3 | 7.841 V DC | Unstable | 12/16/2025 12:14:17.2
16 | 9.479 V DC | 12/16/2025 12:14:17.2 | 0:00:04.8 | 12/16/2025 12:14:21.6 | 9.552 V DC | 9.512 V DC | 12/16/2025 12:14:17.4 | 9.414 V DC | Stable | 12/16/2025 12:14:22.1
17 | 9.555 V DC | 12/16/2025 12:14:22.1 | 0:00:07.1 | 12/16/2025 12:14:29.0 | 9.579 V DC | 9.552 V DC | 12/16/2025 12:14:22.4 | 9.499 V DC | Interval | 12/16/2025 12:14:29.2
18 | 9.530 V DC | 12/16/2025 12:14:29.2 | 0:00:35.7 | 12/16/2025 12:15:04.4 | 9.609 V DC | 9.580 V DC | 12/16/2025 12:14:43.4 | 9.501 V DC | Stable | 12/16/2025 12:15:04.9
19 | 8.881 V DC | 12/16/2025 12:15:04.9 | 0:00:00.9 | 12/16/2025 12:15:05.6 | 9.464 V DC | 8.584 V DC | 12/16/2025 12:15:05.2 | 7.941 V DC | Unstable | 12/16/2025 12:15:05.8
20 | 7.954 V DC | 12/16/2025 12:15:05.8 | 0:00:01.1 | 12/16/2025 12:15:06.5 | 7.967 V DC | 7.921 V DC | 12/16/2025 12:15:06.7 | 7.869 V DC | Stable | 12/16/2025 12:15:06.9
21 | 9.210 V DC | 12/16/2025 12:15:06.9 | 0:00:01.5 | 12/16/2025 12:15:08.3 | 9.418 V DC | 8.929 V DC | 12/16/2025 12:15:07.5 | 7.829 V DC | Unstable | 12/16/2025 12:15:08.4
22 | 9.444 V DC | 12/16/2025 12:15:08.4 | 0:00:02.7 | 12/16/2025 12:15:10.8 | 9.515 V DC | 9.490 V DC | 12/16/2025 12:15:08.4 | 9.444 V DC | Stable | 12/16/2025 12:15:11.2
23 | 8.938 V DC | 12/16/2025 12:15:11.2 | 0:00:03.1 | 12/16/2025 12:15:11.9 | 9.402 V DC | 8.499 V DC | 12/16/2025 12:15:13.8 | 7.785 V DC | Unstable | 12/16/2025 12:15:14.3
24 | 9.347 V DC | 12/16/2025 12:15:14.3 | 0:00:01.1 | 12/16/2025 12:15:15.3 | 9.408 V DC | 9.363 V DC | 12/16/2025 12:15:14.4 | 9.297 V DC | Stable | 12/16/2025 12:15:15.4
25 | 9.421 V DC | 12/16/2025 12:15:15.4 | 0:00:03.7 | 12/16/2025 12:15:18.6 | 9.486 V DC | 9.452 V DC | 12/16/2025 12:15:15.5 | 9.365 V DC | Stable | 12/16/2025 12:15:19.1
26 | 8.118 V DC | 12/16/2025 12:15:19.1 | 0:00:03.1 | 12/16/2025 12:15:19.7 | 9.377 V DC | 8.484 V DC | 12/16/2025 12:15:21.6 | 7.772 V DC | Unstable | 12/16/2025 12:15:22.2
27 | 9.328 V DC | 12/16/2025 12:15:22.2 | 0:00:02.8 | 12/16/2025 12:15:24.7 | 9.428 V DC | 9.375 V DC | 12/16/2025 12:15:22.6 | 9.295 V DC | Stable | 12/16/2025 12:15:25.0
28 | 9.434 V DC | 12/16/2025 12:15:25.0 | 0:00:04.2 | 12/16/2025 12:15:29.2 | 9.476 V DC | 9.444 V DC | 12/16/2025 12:15:25.1 | 9.390 V DC | Interval | 12/16/2025 12:15:29.3
29 | 9.478 V DC | 12/16/2025 12:15:29.3 | 0:00:07.0 | 12/16/2025 12:15:35.8 | 9.508 V DC | 9.482 V DC | 12/16/2025 12:15:30.7 | 9.391 V DC | Stable | 12/16/2025 12:15:36.3
30 | 9.373 V DC | 12/16/2025 12:15:36.3 | 0:00:00.1 | 12/16/2025 12:15:36.3 | 9.373 V DC | 9.373 V DC | 12/16/2025 12:15:36.3 | 9.373 V DC | Unstable | 12/16/2025 12:15:36.4
31 | 9.494 V DC | 12/16/2025 12:15:36.4 | 0:00:04.9 | 12/16/2025 12:15:40.7 | 9.525 V DC | 9.513 V DC | 12/16/2025 12:15:37.0 | 9.473 V DC | Stable | 12/16/2025 12:15:41.3
32 | 8.648 V DC | 12/16/2025 12:15:41.3 | 0:00:03.6 | 12/16/2025 12:15:41.9 | 9.388 V DC | 8.646 V DC | 12/16/2025 12:15:43.2 | 7.837 V DC | Unstable | 12/16/2025 12:15:45.0
33 | 9.382 V DC | 12/16/2025 12:15:45.0 | 0:00:03.7 | 12/16/2025 12:15:48.4 | 9.455 V DC | 9.400 V DC | 12/16/2025 12:15:45.4 | 9.299 V DC | Stable | 12/16/2025 12:15:48.7
34 | 9.458 V DC | 12/16/2025 12:15:48.7 | 0:00:00.5 | 12/16/2025 12:15:49.1 | 9.462 V DC | 9.447 V DC | 12/16/2025 12:15:48.9 | 9.400 V DC | Unstable | 12/16/2025 12:15:49.2
35 | 9.361 V DC | 12/16/2025 12:15:49.2 | 0:00:07.0 | 12/16/2025 12:15:55.8 | 9.496 V DC | 9.462 V DC | 12/16/2025 12:15:49.2 | 9.361 V DC | Stable | 12/16/2025 12:15:56.2
36 | 9.498 V DC | 12/16/2025 12:15:56.2 | 0:00:33.0 | 12/16/2025 12:16:28.1 | 9.540 V DC | 9.509 V DC | 12/16/2025 12:16:13.4 | 9.417 V DC | Interval | 12/16/2025 12:16:29.2
37 | 9.497 V DC | 12/16/2025 12:16:29.2 | 0:01:00.0 | 12/16/2025 12:17:23.6 | 9.562 V DC | 9.539 V DC | 12/16/2025 12:17:23.7 | 9.462 V DC | Interval | 12/16/2025 12:17:29.2
38 | 9.537 V DC | 12/16/2025 12:17:29.2 | 0:01:00.1 | 12/16/2025 12:18:21.0 | 9.569 V DC | 9.549 V DC | 12/16/2025 12:17:59.4 | 9.461 V DC | Interval | 12/16/2025 12:18:29.2
39 | 9.566 V DC | 12/16/2025 12:18:29.2 | 0:00:14.5 | 12/16/2025 12:18:42.8 | 9.572 V DC | 9.553 V DC | 12/16/2025 12:18:40.5 | 9.493 V DC | Stable | 12/16/2025 12:18:43.7
40 | 9.423 V DC | 12/16/2025 12:18:43.7 | 0:00:03.1 | 12/16/2025 12:18:44.4 | 9.443 V DC | 8.531 V DC | 12/16/2025 12:18:46.3 | 7.820 V DC | Unstable | 12/16/2025 12:18:46.9
41 | 9.352 V DC | 12/16/2025 12:18:46.9 | 0:00:01.5 | 12/16/2025 12:18:48.2 | 9.444 V DC | 9.400 V DC | 12/16/2025 12:18:46.9 | 9.352 V DC | Stable | 12/16/2025 12:18:48.4
42 | 9.451 V DC | 12/16/2025 12:18:48.4 | 0:00:08.9 | 12/16/2025 12:18:56.0 | 9.518 V DC | 9.483 V DC | 12/16/2025 12:18:48.5 | 9.398 V DC | Stable | 12/16/2025 12:18:57.2
43 | 9.519 V DC | 12/16/2025 12:18:57.2 | 0:00:32.0 | 12/16/2025 12:19:27.3 | 9.550 V DC | 9.523 V DC | 12/16/2025 12:18:58.9 | 9.435 V DC | Interval | 12/16/2025 12:19:29.2
44 | 9.545 V DC | 12/16/2025 12:19:29.2 | 0:00:21.1 | 12/16/2025 12:19:49.9 | 9.557 V DC | 9.537 V DC | 12/16/2025 12:19:45.3 | 9.454 V DC | Stable | 12/16/2025 12:19:50.3
45 | 8.486 V DC | 12/16/2025 12:19:50.3 | 0:00:03.4 | 12/16/2025 12:19:50.9 | 9.415 V DC | 8.585 V DC | 12/16/2025 12:19:52.9 | 7.790 V DC | Unstable | 12/16/2025 12:19:53.8
46 | 9.385 V DC | 12/16/2025 12:19:53.8 | 0:00:03.0 | 12/16/2025 12:19:56.6 | 9.464 V DC | 9.424 V DC | 12/16/2025 12:19:53.9 | 9.359 V DC | Stable | 12/16/2025 12:19:56.8
47 | 9.469 V DC | 12/16/2025 12:19:56.8 | 0:00:18.9 | 12/16/2025 12:20:15.0 | 9.527 V DC | 9.493 V DC | 12/16/2025 12:19:57.6 | 9.419 V DC | Stable | 12/16/2025 12:20:15.7
48 | 9.275 V DC | 12/16/2025 12:20:15.7 | 0:00:02.9 | 12/16/2025 12:20:16.4 | 9.404 V DC | 8.456 V DC | 12/16/2025 12:20:18.3 | 7.798 V DC | Unstable | 12/16/2025 12:20:18.6
49 | 9.287 V DC | 12/16/2025 12:20:18.6 | 0:00:01.3 | 12/16/2025 12:20:19.7 | 9.396 V DC | 9.352 V DC | 12/16/2025 12:20:18.6 | 9.287 V DC | Stable | 12/16/2025 12:20:19.9
50 | 9.401 V DC | 12/16/2025 12:20:19.9 | 0:00:05.9 | 12/16/2025 12:20:25.6 | 9.475 V DC | 9.435 V DC | 12/16/2025 12:20:20.1 | 9.346 V DC | Stable | 12/16/2025 12:20:25.8
51 | 9.476 V DC | 12/16/2025 12:20:25.8 | 0:00:03.3 | 12/16/2025 12:20:26.2 | 9.478 V DC | 8.735 V DC | 12/16/2025 12:20:28.6 | 7.805 V DC | Unstable | 12/16/2025 12:20:29.2
52 | 7.823 V DC | 12/16/2025 12:20:29.2 | 0:00:00.1 | 12/16/2025 12:20:29.2 | 7.823 V DC | 7.823 V DC | 12/16/2025 12:20:29.2 | 7.823 V DC | Interval | 12/16/2025 12:20:29.3
53 | 7.793 V DC | 12/16/2025 12:20:29.3 | 0:00:00.9 | 12/16/2025 12:20:30.0 | 9.317 V DC | 8.878 V DC | 12/16/2025 12:20:29.4 | 7.778 V DC | Unstable | 12/16/2025 12:20:30.2
54 | 9.333 V DC | 12/16/2025 12:20:30.2 | 0:00:04.5 | 12/16/2025 12:20:34.4 | 9.427 V DC | 9.379 V DC | 12/16/2025 12:20:30.4 | 9.303 V DC | Stable | 12/16/2025 12:20:34.7
55 | 9.430 V DC | 12/16/2025 12:20:34.7 | 0:00:43.2 | 12/16/2025 12:21:15.4 | 9.506 V DC | 9.469 V DC | 12/16/2025 12:20:53.8 | 9.384 V DC | Stable | 12/16/2025 12:21:17.9
56 | 9.507 V DC | 12/16/2025 12:21:17.9 | 0:00:11.4 | 12/16/2025 12:21:26.7 | 9.512 V DC | 9.496 V DC | 12/16/2025 12:21:18.2 | 9.431 V DC | Interval | 12/16/2025 12:21:29.2
57 | 9.511 V DC | 12/16/2025 12:21:29.2 | 0:00:03.7 | 12/16/2025 12:21:32.0 | 9.517 V DC | 9.509 V DC | 12/16/2025 12:21:30.0 | 9.472 V DC | Stable | 12/16/2025 12:21:32.9
58 | 8.405 V DC | 12/16/2025 12:21:32.9 | 0:00:03.5 | 12/16/2025 12:21:33.5 | 9.383 V DC | 8.497 V DC | 12/16/2025 12:21:35.6 | 7.801 V DC | Unstable | 12/16/2025 12:21:36.5
59 | 9.361 V DC | 12/16/2025 12:21:36.5 | 0:00:05.7 | 12/16/2025 12:21:41.7 | 9.450 V DC | 9.410 V DC | 12/16/2025 12:21:36.6 | 9.354 V DC | Stable | 12/16/2025 12:21:42.2
60 | 9.454 V DC | 12/16/2025 12:21:42.2 | 0:00:05.9 | 12/16/2025 12:21:47.7 | 9.477 V DC | 9.455 V DC | 12/16/2025 12:21:44.2 | 9.400 V DC | Stable | 12/16/2025 12:21:48.1
61 | 9.224 V DC | 12/16/2025 12:21:48.1 | 0:00:03.8 | 12/16/2025 12:21:51.7 | 9.329 V DC | 8.597 V DC | 12/16/2025 12:21:50.8 | 7.770 V DC | Unstable | 12/16/2025 12:21:52.0
62 | 9.339 V DC | 12/16/2025 12:21:52.0 | 0:00:02.8 | 12/16/2025 12:21:54.4 | 9.405 V DC | 9.382 V DC | 12/16/2025 12:21:52.0 | 9.339 V DC | Stable | 12/16/2025 12:21:54.8
63 | 8.166 V DC | 12/16/2025 12:21:54.8 | 0:00:03.5 | 12/16/2025 12:21:55.4 | 9.294 V DC | 8.511 V DC | 12/16/2025 12:21:57.3 | 7.741 V DC | Unstable | 12/16/2025 12:21:58.3
64 | 9.291 V DC | 12/16/2025 12:21:58.3 | 0:00:02.5 | 12/16/2025 12:22:00.4 | 9.358 V DC | 9.333 V DC | 12/16/2025 12:21:58.3 | 9.291 V DC | Stable | 12/16/2025 12:22:00.8
65 | 8.299 V DC | 12/16/2025 12:22:00.8 | 0:00:03.1 | 12/16/2025 12:22:02.2 | 9.223 V DC | 8.344 V DC | 12/16/2025 12:22:03.4 | 7.705 V DC | Unstable | 12/16/2025 12:22:03.9
66 | 9.209 V DC | 12/16/2025 12:22:03.9 | 0:00:02.2 | 12/16/2025 12:22:05.8 | 9.307 V DC | 9.257 V DC | 12/16/2025 12:22:04.3 | 9.168 V DC | Stable | 12/16/2025 12:22:06.1
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

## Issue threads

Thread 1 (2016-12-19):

Power Down Pin shuffle

dHutchings, 2016-12-19:
Investigated additional power down modes.  can get a good .118mA average power draw from the Micro, using powerDown().  (better than 19mA from idle())

However...

1. Power down library doesn't correctly disable BOD for ATMEGA32u4.  Fix / update the library.
2. Power up can only be accomplished by interrupts 0:3, therefore pins 3,2,1,0
3. Power dissipation changes based on which pins are being used.  Pins 3 & 2 are the best, at .1mA
4. Those pins are already in use with i2C.

TO-do on this issue:

1. Fix BOD in power down library.  Maybe that'll fix things.
2. If not, investigate a bit-banging software i2c.
3. If software i2c good:
4. Move software i2c to other DIOs
5. Attach INT to 2 or 3 (disconnect from 7), add 4th button to other pin.
3. If software i2c not good:
4. Switch INT and USR1/2.

Change INT pin to 2 or 3, since only those two

dHutchings, 2016-12-19:
Update:

cannot fix BOD.  Requires flashing fuses, which the pins aren't broken out to do.

dHutchings, 2016-12-29:
Closed in new PCB rev.

Closed 2016-12-29.

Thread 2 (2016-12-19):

Low Power lockout Chip

dHutchings, 2016-12-19:
get & test a low-power lockout chip, for use on the battery line.

dHutchings, 2016-12-29:
TPS3803-01DCKR

dHutchings, 2016-12-29:
integrated into rev B

dHutchings, 2016-12-29:
TPS3710DDCR.  Most other TI and not-TI chips have 7V maximum VCC, i want this to run right of battery...

Closed 2016-12-29.

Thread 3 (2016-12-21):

Rev A erratta

dHutchings, 2016-12-21:
Erratta just to get the thing minimally working...

- [x] Switch D and S of mosfet
- [ ] more capacitance: 500mF at least, 1F preferred
- [ ] switch holes aren't right size
- [ ] silkscreen problems
- [x] add part for MOSFET bolt to BOM
- [x] test points for V1, V2, COIL
- [x] right-angle USB
- [x] footprint for 0805s
- [x] breakout for int
- [x] circuit for non-invering addition amp is wrong: you swapped + and - inputs

dHutchings, 2016-12-21:
- [ ] Flip 5V / GND pinheader.

dHutchings, 2016-12-29:
From some decisions:
- [ ] change solar charging position to USB connection position.
- [ ] use this 5V step down regulator: https://www.pololu.com/product/2858

dHutchings, 2016-12-29:
- [ ] smaller / cheaper switch?

Closed 2016-12-30.

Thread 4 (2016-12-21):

Some decisions

dHutchings, 2016-12-21:
Ditch Solar charging hopes
use 6AA's (https://www.pololu.com/product/1155/specs)
change solar charging position to USB connection position.
use this 5V step down regulator: https://www.pololu.com/product/2858

dHutchings, 2016-12-29:
Implemented in part of rev B pcb.

Closed 2016-12-29.

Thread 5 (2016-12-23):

Mechanical Rev D

dHutchings, 2016-12-23:
Info for next mechanical revision...

- [ ] #4-40 standoff as shaft isn't cutting it.  Slightly bent shafts really cause pendulum to stop performing well.  Either get a strong standoff, some better shaft solution, or create an extra mounting point offset from pillar so that a shoulder bolt can be used alone.
- [ ] 3/8" base with batteries seems like it'll be heavy enough

Closed 2016-12-31.

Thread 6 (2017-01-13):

Mech Rev D issues

dHutchings, 2017-01-13:
- [x] Pillar Assy Drawing needs correct label: 2x washer -> 3x washer
- [x] Pendulum Drawing: note about filing washer down to .022"
- [x] 5 washers between pendulum links, not 4
- [x] Add final dimmension to bearing_offset drawing
- [x] Mounting holes for battery holder are 2.266" apart.. either the part itself or the base plate is messedup
- [x] The base plate has the wrong diameter holes for the battery holder: should be 8-32 (tapped or clearance?)
- [x] Look carefully at the plate mounting options... may be best to put it into tapped holes.
- [x] add a second washer between the bearing_offset and the pillar.
- [x] add material notes to every drawing

dHutchings, 2017-01-13:
add holes for zipties to pillar, for wire management.  1/8" will do fine for small zipties.

dHutchings, 2017-01-14:
- [ ] Move battery holder so it is no more than 0.35" away from edge for USB connector

Closed 2017-01-15.

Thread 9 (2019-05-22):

Lower Power / Cost

dHutchings, 2019-05-22:
- [ ] Consider using zeiner diodes for low-cost voltage rails for the Comparator / Voltage adder circuit.  https://www.electronics-tutorials.ws/diode/diode_7.html

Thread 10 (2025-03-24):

Electrical Changes

dHutchings, 2025-03-24:
- [ ] Do spreadsheet for power budget (current: 2x DAC 0.4 mA, MCP6002 op-amp: 0.4 mA, uC 0.07 mA) estimating how long the things will run on AA's
- [ ] Go with new op-amp: MCP6142
- [ ] The current circuit for the switching regulator saps power from the AA's as the regulator is always on.  Do something about this!
- [ ] Switch u3 (the dac generating v1) to LM4040 from tpod.  (LM4040X20I, for 2.0485V, which is close to the currently commanded 2.0V).  LM4040 draws ~60 uA, so we'd be saving ~140uA per DAC.  I was hoping to do better...  but pretty much all the references out there don't draw less than 60ish.  OOR we could spend a bit more money, about $1.40 ea, to get the REF35 (probably REF35205 and REF35160) which each draw ~0.6 uA (!).  It's not as cheap as the LM4040 ($0.40), but the origial DAC is about $1, so it's only $.40 (ea) more for saving 398 uA.  Might be worth it.

dHutchings, 2025-03-24:
On the switching regulator:

The original 5V 2.5A regulator:
https://www.pololu.com/product/2858  quiescent current of ~800 uA at battery voltage... and costs ~$11 in 2025

New 5V low-current regulators:
https://www.pololu.com/product/5373 can produce the needed 5V with quiscent currents in the tens of uA(!!)
https://www.pololu.com/product/5433 is only a little bit worse, in the 100 uA territory.

**if we DO change the coil to be a lower resistance**..
What about two regulators?  One for the logic, one for the coil.
Use a boost converter, like https://www.pololu.com/product/4945, as a smaller / cheaper source of (say, 12V).  12V 0.5 Amp ~= 5V 2.5A in terms of power... for the coil.
We can cascade the two regulators so that the 12V powers the 5V.
Or, we can have the 5V powered from the main power rail - BUT - have the enable pin driven low by raw USB power and then have a diode from USB power the 5V logic.

dHutchings, 2025-04-06:
On the auto-reboot feature

TPL5111 will do the trick, but it will take 3 DIO to do it.  We will use the TPL5111 in one-shot mode, most similar to fig 12.  It has to be in one-shot mode since in timer mode the counter does not reset when 'DONE' is asserted, so we could hypothetically get a reset at the wrong time.

In one shot mode:
1) We drive Delay / DRV high for 20 ms (!) to start the timer.
2) chip drives DRVn high immediately,
then either
A1) We drive done, and
A2) DRVn is driven low (it looks like pretty quickly, within 100 ns according to datasheet)
OR
B1) timer elapses
B2) DRVn driven low.

So, what we can do is this:
- hook up reset to DRVn falling.
- every time we begin to push the pendulum, drive  DONE high / low.  Then, start driving Delay high.
- when we are done pushing the pendulum & 20 ms has gone by, drive delay low
- Then the timer starts
- If we ever drive because

dHutchings, 2025-04-06:
- [ ] Label the fact that we're using non-standard i2c pins on the schematic
- [ ] Label i2c addresses on the schematic
- [ ] Change the soft i2c lines to something other than 7, because I need that interrupt pin for the restart functionality: https://roboticsbackend.com/arduino-interrupts/
- [ ]

dHutchings, 2025-04-12:
- [ ] Use https://www.digikey.com/en/products/detail/keystone-electronics/4881/6234710 for PCB mounting.  negates need for threaded holes on pillar.

dHutchings, 2025-06-17:
-  [ ] Use 555 Timer for the reset.  Its better, but not lower power, it does what I want more.
- [ ]

dHutchings, 2025-06-17:
I should just route the board as D1, ship it.  I've done everything but re-working the battery powered / coil shtuff.

Once I'm back & I am making coils, then, then, I can deal with redoing that last bit.

dHutchings, 2025-06-17:
- [ ] the DAC:

Might just be easiest to switch to MCP4728.  It's an i2c 4-dac, 2 of which can be powered down.  There's an adafruit library.  It looks like we hit ~400 uA with only two DACs on.  That's a savings of 800 uA, compared to what I currently have (0.8 mA)

dHutchings, 2025-07-08:
- [ ] On the new board:
With everything installed, we're drawing ~30mA on startup / restart, ~0.943 ma when the 555 timer is not yet triggered / 1.443 mA when the 555 IS triggered.

10K pull up / 5V -> I = V/R = 5/10k = 500 uA.  Basically, all of that extra current is eaten up by the pull-up.

-[ ] TODO: Change all pullups to 100k (50uA) or 1M (5uA), each pull-up is currently costing us 500uA.  There are pull-ups on R7, R10,  (easy to change), R5 R6 (harder to change??)....

I tested 1M --> Just fine.

- [ ] Finally get around to resistor arrays.  Fortunately, sparkfun has a footprint for 0805 4x arrays that ought to work well.
-->

dHutchings, 2025-07-09:
- [ ] Consider BEMF measurement via a peak-detection circuit.
Currently basing this off of the EEVBLOG with 2 op-amps & 1 diode.

turn diode backwards b/c detecting negative pulses, not positive.
Use 200 nF caps.
(unusually)  use 100k ohm resistor in series with diode to reduce the shuddering seen in this image:
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

Use 10M ohm resistor to 5V to reset.

Current breadboard implementation works aight (Yellow), although the resistor (even a huge 10M) does cause the value to fall over time.  Simply put, the requirement to hold the peak for several seconds is hard to do with a resistor to reset the value.

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

Consider using MOSFET instead to do the reset... the mosfet could be hooked up to DRIVE.

dHutchings, 2025-07-18:
- [ ] ToDo when I get back rev D2:
I think we don't actually need Q4 as a reset.  Instead, wire it directly (with a solder jumper) to a dio, leave that DIO floating for normal operation / write it high to reset.

dHutchings, 2025-07-25:
- [ ] Todo when I get back rev D2:
Do I need the PNP transistor?  I think I can do it with a MOSFET, or even, straight with the DIO (since the DIO ought to be strong enough to discharge the cap)

dHutchings, 2025-08-09:
- Power draw as of commit ba708d690476de969bf085fa17b655e4501ac4fd on modified D2 hardware:
Drawing (according to fluke 289) 0.0101 Amps @ 9V + 1.11 ma @5V.
Assuming the 5V regulator is 90% efficient AND draws 15uA @ 9V quiescent current... total power is:
0.0101 A * 9V + (1/0.9)*1.11 mA * 5V +  15uA * 9V =  0.0972 Watts

the rev C elelectronics draws:
5V @ 0.0275 Amps = 0.1375 Watts.

It looks like this system (right now) draws 30% less power!  w00t!

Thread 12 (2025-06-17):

Software Issues

dHutchings, 2025-06-17:
- [ ] Get around to getting a DAC library and using clever arduino inheretince issues to overwrite Wire.h:

https://arduino-craft-corner.de/index.php/2023/11/29/replacing-the-wire-library-sometimes/
https://github.com/felias-fogg/FlexWire?tab=readme-ov-file

dHutchings, 2025-08-06:
- [ ] Get around to storing power settings in EEPROM.

dHutchings, 2025-08-08:
- [ ] may be possible to edit the Watchdog timer to run for times less than 16ms: https://forum.arduino.cc/t/wdt-watchdog-timer-code/353610/10
If I do that, then, we can use the power-down library for short timeframes, allowing us to be powered-down during the MOSFET on time.  That could save power!
As a guess, there are about 3 pushes a second --> so the uC is on for 30ms per 1000ms.  30ms at 20ma = 0.6 s-ma.  500 uA for 970 ms per 1000 ms --> 0.485 s-ma ---> We are consurming nearly as much power when the uC is on for 30ms then when its off for the rest of the time!

dHutchings, 2025-08-09:
- After all the powerdown improvements:
I'm drawing 0.77 uA when the pendulum isn't moving ... and time average (when the pendulum IS moving) i'm drawing 1.14 mA on the 5V line.  This, is pretty good.  I cant measure (TODO- can I?) the time average for just the logic when the pendulum is moving, but I'm beating the long-term average when pendulum isn't moving & I think there are good reasons to believe that I'm saving a lot of power when it IS moving (because of better timing / precision_Idle / etc)

dHutchings, 2025-08-10:
ADC 7 - PF7 - A0
ADC 6 - PF6 - A1
ADC 5 - PF5 - A1
ADC 4 - PF4 - A3

(inaccessible)
ADC 1 - PF1 - A4
ADC 0 - PF0 - A5

ADC 3 - PF1
ADC 0 - PF 0

AIN0D ---> Comparator?

ADC13 - PB6 - D10#
ADC12 - PB5 - D9# / A8
ADC11 - PB4 - D8
ADC10 - PD7 - D6# / A7
ADC9 - PD6 - D5#
ADC8 - PD4 - D4 / A6

Of these, I use as analog inputs A0 A1 (just during boot - the CC pins)
And 4 / A6 - BEMF sensing

suggests that I should set
DIDR0 |= _BV(ADC7D) | _BV(ADC6D);
DIDR2 |= _BV(ADC8D);

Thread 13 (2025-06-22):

Rev D1 Erratta

dHutchings, 2025-06-22:
- [x] GND traveling through small pour right below C6

dHutchings, 2025-06-29:
- [ ] didn't use the right gerber to export, silkscreen is missing values.

dHutchings, 2025-06-29:
- [ ] Use a less OP mosfet.

dHutchings, 2025-06-29:
- [ ] Add silkscreen labels for the debug connector.  And, add AUTO_RESTART to the debug connector.

dHutchings, 2025-06-30:
- [ ] right now, the pulse detector fires if we are high for more than about 250 ms.  The math says it should be 4.4 seconds.  Something's wrong --> Either:
The "Detailed design procedure" is missing something (e.g. find a better design guide)
I soldered something wrong.
Something else is wrong.

Closed 2025-07-22.

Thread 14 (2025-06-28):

Mechanical changes

dHutchings, 2025-06-28:
- [ ] Consider using 92510A421 rather than stack of washers for the links between the first and second link.

dHutchings, 2025-07-24:
- [ ] Check into the CAD of the APM.  It looks like the APMs with USBC connectors are longer than the microUSB, thus causing issues with placement / being unable to plugin.

dHutchings, 2025-07-31:
- [ ] For next time:
Consider 90318A590 (shoulder screws with super-low head).  They're only a dollar (per) more, but, this could reduce or get rid of the stack of washers / the locknut / the magnet <-> coil gap.

dHutchings, 2025-08-05:
- [ ] BOM: bad order from MMC, ordered the wrong steel standoff.

dHutchings, 2025-08-10:
- [ ] The Setscrew is anywhere between 40 and 60 thouh shorter than the hole.

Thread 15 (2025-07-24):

Rev D2 Erratta

dHutchings, 2025-07-24:
- [ ] Consider Parts re-numbering.
- [ ] The Op-amps should be ICs, not Us,

dHutchings, 2025-07-24:
try TSW-150-07-T-S and SLW-150-01-T-S for shorter pin headers.

dHutchings, 2025-08-06:
- [ ] We have a 29mV drop across the the P-MOS Q1.  Is that good?  Bad?  IDK.   (0.2% power loss in the mosfet - ~15V across the coil, 29mV across the mosfet).  Do hte Math / Compare this to the previous revision to see if we did better or worse on that.

dHutchings, 2025-08-06:
- [ ] See Quickprint22.  It definately seems that, even with super-low threshold voltage, there are times (e.g. when I'm already moving very fast) where the APM can't wake up quickly enough, and misses most of hte effective BEMF range for the magnet.  When I'm slower, it matters less.
- [ ] IDEA: If we can work out a relationship: PEAK BEMF vs BEMF width, we can probably dynamically choose our pushing time to avoid wasting power.

dHutchings, 2025-08-07:
Notes from previous pendulum:
- the op-amp as a comparator has a swing time from high to low of 100 us - the new one is approx 2ms.

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

dHutchings, 2025-08-07:
Colors for all of the o-scope probes (unless otherwise comented):

Cyan: COIL
Purple: SHIFT
Yellow: V1 (threshold for the comparator)
Dark Blue: INT (comparator out)

dHutchings, 2025-08-08:
- The PMOS has died once.  Just keep an eye on it... if it happens again, might not be a bad idea to switch to something bigger or more robust.  Maybe finding something bigger / more robust might also help with the gate issue...?

dHutchings, 2025-08-08:
- [ ] Go with a much smaller, or possibly 0 ohm, R3A for the resistor in the BEMF measurement circuit.

Quickprint 27 thru 29 shows that we have now.  No stepwise problem, BUT, the peak is so fast that sometimes we miss it.  Because hte 22k ohm + .1uF cap form an RC network that is too busy charging up.

Quickprint 31, 32, shows what we get when we short that resistor with tweezers (boy, is that hard to do).  Stepwise _is_ a problem, but, not *THAT* much of one.

dHutchings, 2025-08-08:
- [ ] MIrror the coil driver sch... it violates "input on left output on right" convention.

dHutchings, 2025-08-08:
- [  ] Idea: use the 22k as i2c pullups?  Those are fine i2c values and would let you double-dip.

dHutchings, 2025-08-08:
- [ ] N$1 should have a test point

dHutchings, 2025-08-08:
Frankley, [MCP6232](https://www.digikey.com/en/products/detail/microchip-technology/MCP6232T-E-SN/716084) might be a good idea:

It still saves power compared to MCP6002 (20uA per op-amp, rather than 100) - not as much as the MCP6142, BUT, Its got a massively larger slew rate (0.15 V/us rather than 0.003) which might buy us out of both the comparator and stepwise problems.

dHutchings, 2025-08-09:
- [ ] Get rid of Q4 per developed procedure on different issue.

dHutchings, 2025-08-09:
- 15V switching regulator works great, the quiescient curve is approx what the pololu site says & it doesn't dip at all when pushing the coil.
- [ ] Do not need the big electolytic cap.

dHutchings, 2025-08-09:
- [ ] Change the diode to shotky, the silicon diode does sometimes miss peaks (can't keep up) that hte shotky does a better job on.  Still, the op-amp will save the day.  (Quickprint 59)

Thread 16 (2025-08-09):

Look into APM Fuses

dHutchings, 2025-08-09:
I think we can change the fuse settings to reboot and restart faster from sleep modes than we currently are.

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

Kind of confused since the arduino ide's default is FF, which means an rc and 64 ms start-up??  I'm confused.

dHutchings, 2025-08-10:
https://www.partsnotincluded.com/sparkfun-pro-micro-with-usb-a/

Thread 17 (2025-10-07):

Pressing the slow down button too readily resets the pendulum.

dHutchings, 2025-10-07:

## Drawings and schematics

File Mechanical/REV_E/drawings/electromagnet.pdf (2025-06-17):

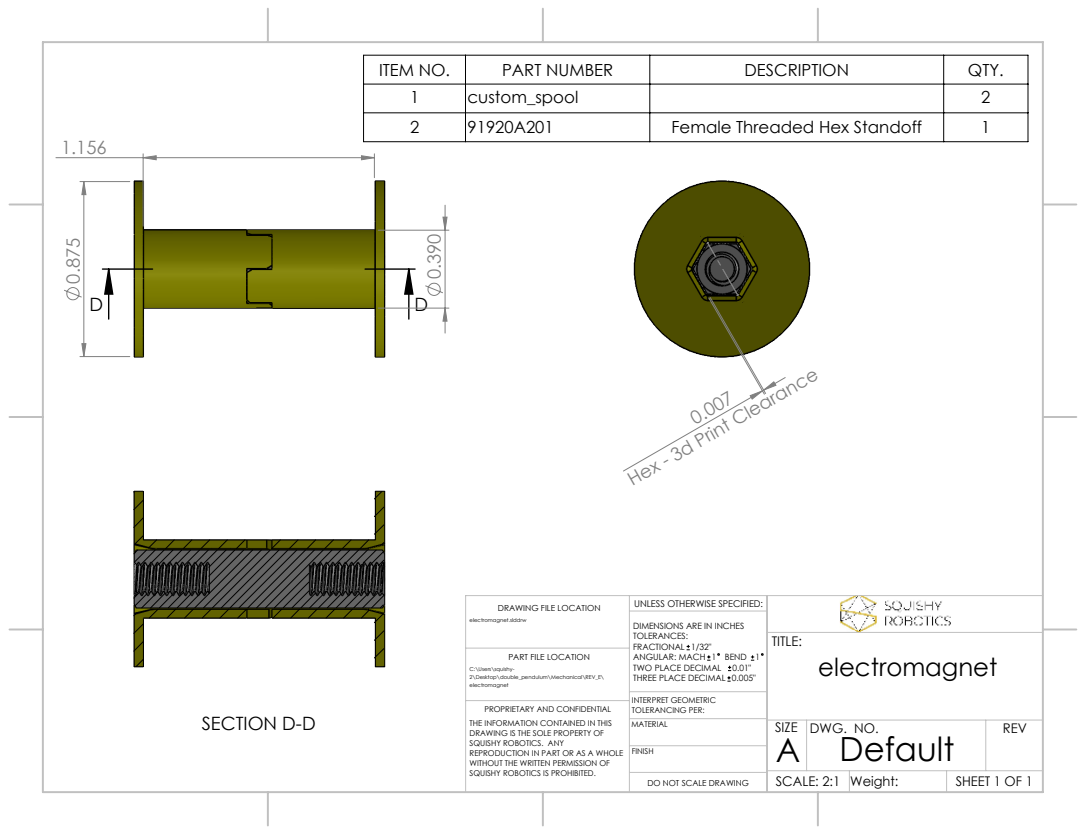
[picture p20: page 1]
SECTION D-D; SCALE: 2:1; Weight:; SHEET 1 OF 1; DWG. NO.; REV; INTERPRET GEOMETRIC TOLERANCING PER:

ITEM NO. | PART NUMBER | DESCRIPTION | QTY.
1 | custom_spool | | 2
2 | 91920A201 | Female Threaded Hex Standoff | 1

Hex - 3d Print Clearance

UNLESS OTHERWISE SPECIFIED:

DRAWING FILE LOCATION

DIMENSIONS ARE IN INCHES
TOLERANCES:
FRACTIONAL 1/32"
ANGULAR: MACH 1 BEND 1
TWO PLACE DECIMAL 0.01"
THREE PLACE DECIMAL 0.005"

PART FILE LOCATION

PROPRIETARY AND CONFIDENTIAL
THE INFORMATION CONTAINED IN THIS
DRAWING IS THE SOLE PROPERTY OF
SQUISHY ROBOTICS. ANY
REPRODUCTION IN PART OR AS A WHOLE
WITHOUT THE WRITTEN PERMISSION OF
SQUISHY ROBOTICS IS PROHIBITED.

DO NOT SCALE DRAWING

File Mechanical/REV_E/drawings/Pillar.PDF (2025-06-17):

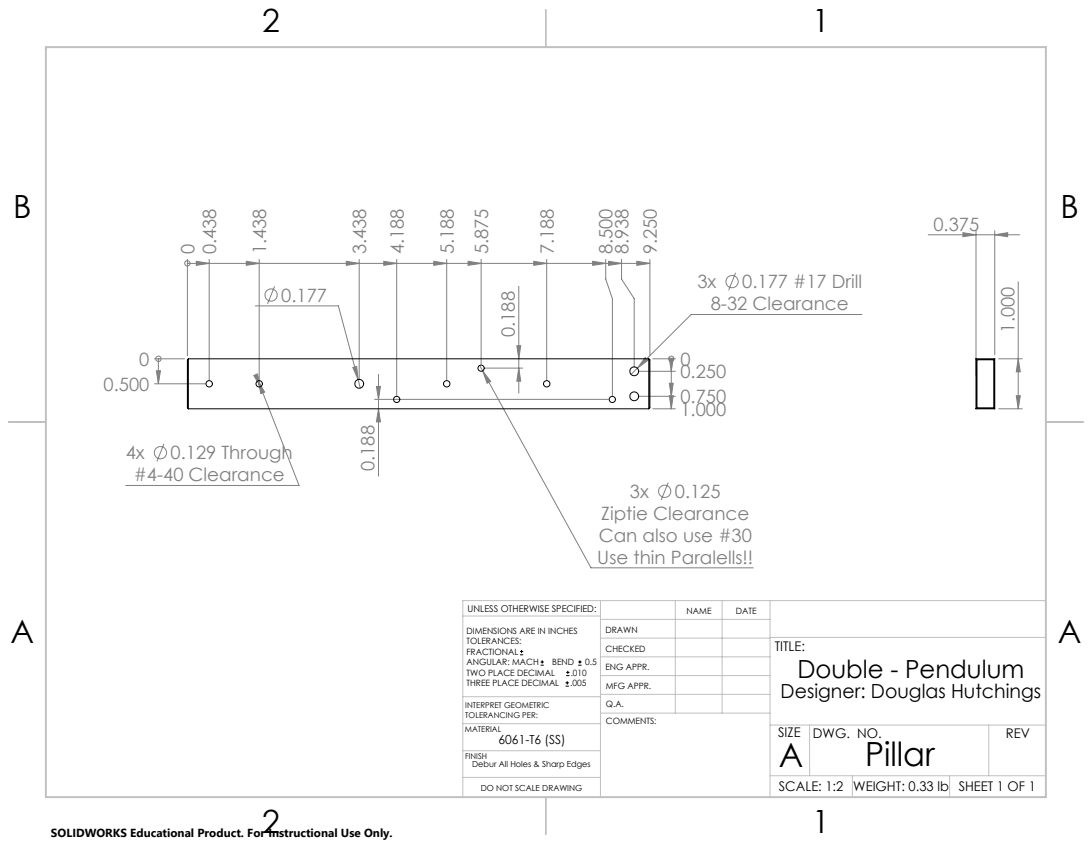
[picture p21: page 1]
3x 0.177 #17 Drill 8-32 Clearance; 4x 0.129 Through #4-40 Clearance; SHEET 1 OF 1; SCALE: 1:2; WEIGHT: 0.33 lb; DWG. NO.; REV

Ziptie Clearance
Can also use #30
Use thin Paralells!!

UNLESS OTHERWISE SPECIFIED: | | NAME | DATE
DIMENSIONS ARE IN INCHES TOLERANCES: FRACTIONAL ANGULAR: MACH BEND 0.5 TWO PLACE DECIMAL .010 THREE PLACE DECIMAL .005 | DRAWN

CHECKED | | | TITLE: Double - Pendulum Designer: Douglas Hutchings

ENG APPR.
MFG APPR.

INTERPRET GEOMETRIC TOLERANCING PER: | Q.A.

FINISH
Debur All Holes & Sharp Edges

DO NOT SCALE DRAWING

SOLIDWORKS Educational Product. For Instructional Use Only.

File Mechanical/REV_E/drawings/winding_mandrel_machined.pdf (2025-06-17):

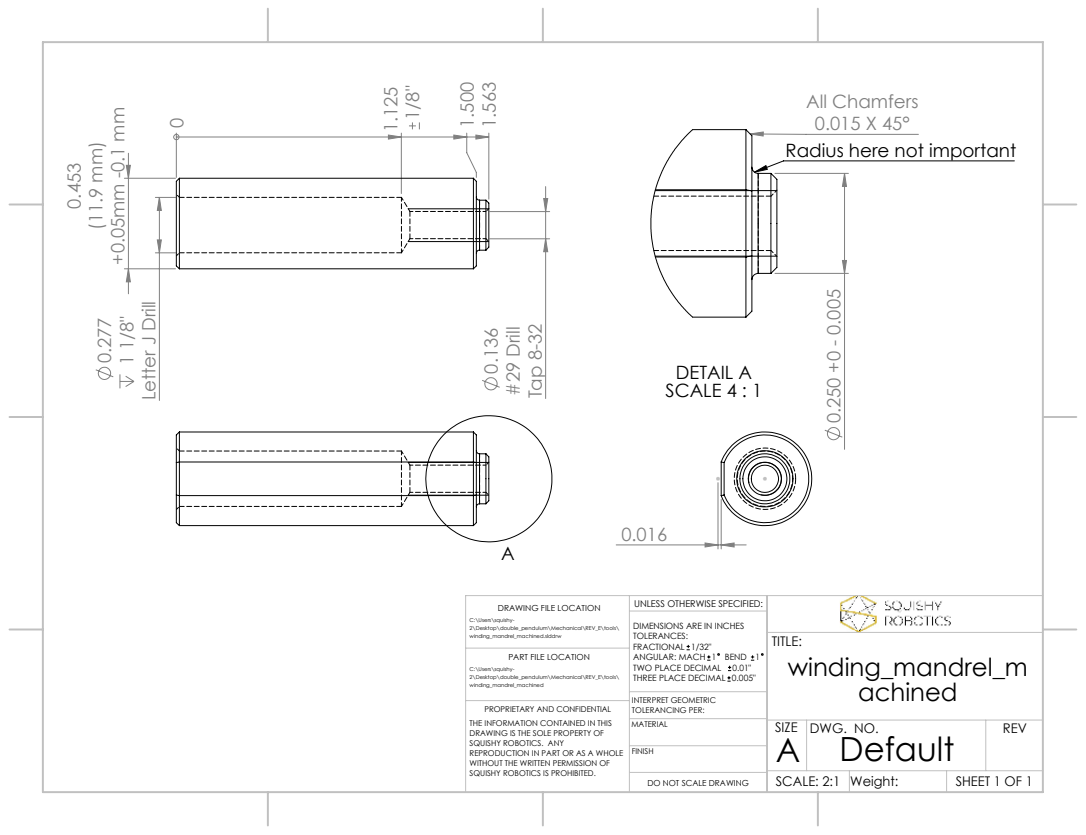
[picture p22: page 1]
Letter J Drill; #29 Drill; Tap 8-32; DETAIL A SCALE 4 : 1; SCALE: 2:1; Weight:; SHEET 1 OF 1; DWG. NO.; REV; 1 BEND; INTERPRET GEOMETRIC TOLERANCING PER:

All Chamfers
Radius here not important

UNLESS OTHERWISE SPECIFIED:

DRAWING FILE LOCATION

C:\Users\squishy-
2\Desktop\double_pendulum\Mechanical\REV_E\tools\
winding_mandrel_machined.slddrw

DIMENSIONS ARE IN INCHES
TOLERANCES:
FRACTIONAL 1/32"
ANGULAR: MACH
TWO PLACE DECIMAL 0.01"
THREE PLACE DECIMAL 0.005"

PART FILE LOCATION

winding_mandrel_machined

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

DO NOT SCALE DRAWING

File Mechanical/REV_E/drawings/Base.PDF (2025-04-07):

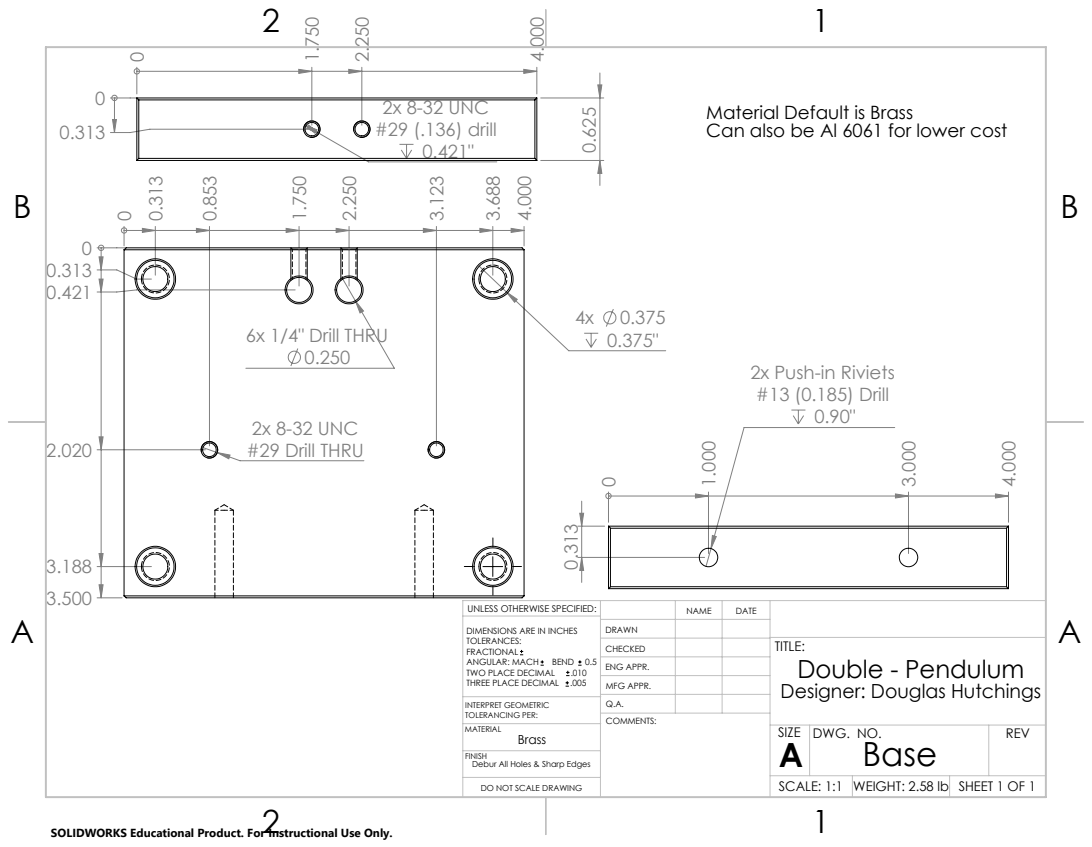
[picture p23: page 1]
6x 1/4" Drill THRU; 2x 8-32 UNC #29 Drill THRU; 2x 8-32 UNC #29 (.136) drill; 2x Push-in Riviets #13 (0.185) Drill; SHEET 1 OF 1; SCALE: 1:1; WEIGHT: 2.58 lb; DWG. NO.; REV

Material Default is Brass
Can also be Al 6061 for lower cost

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

CHECKED | | | TITLE: Double - Pendulum Designer: Douglas Hutchings

ENG APPR.
MFG APPR.

INTERPRET GEOMETRIC TOLERANCING PER: | Q.A.

FINISH
Debur All Holes & Sharp Edges

DO NOT SCALE DRAWING

SOLIDWORKS Educational Product. For Instructional Use Only.

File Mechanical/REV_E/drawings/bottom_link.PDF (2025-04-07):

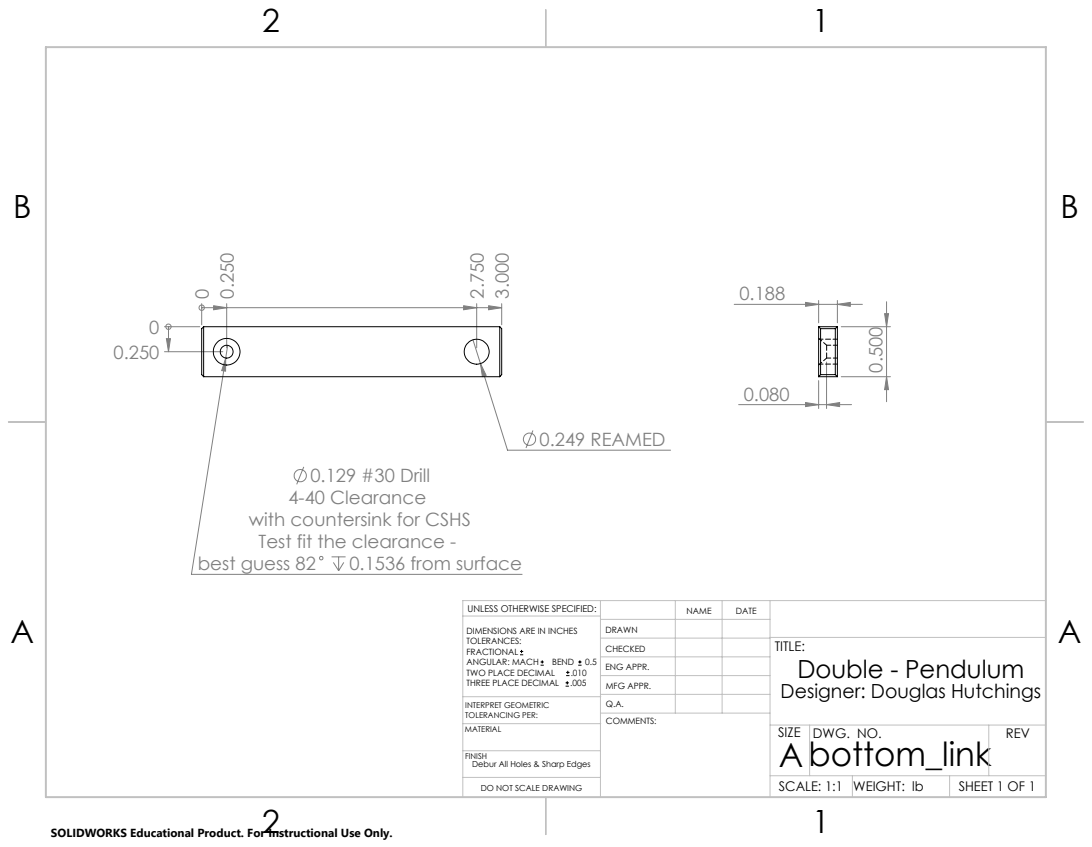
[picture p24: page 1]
best guess 82; 0.1536 from surface; 0.249 REAMED; SHEET 1 OF 1; SCALE: 1:1; WEIGHT: lb; DWG. NO.; REV

0.129 #30 Drill
4-40 Clearance
with countersink for CSHS
Test fit the clearance -

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

CHECKED | | | TITLE: Double - Pendulum Designer: Douglas Hutchings

ENG APPR.
MFG APPR.

INTERPRET GEOMETRIC TOLERANCING PER: | Q.A.

FINISH
Debur All Holes & Sharp Edges

DO NOT SCALE DRAWING

SOLIDWORKS Educational Product. For Instructional Use Only.

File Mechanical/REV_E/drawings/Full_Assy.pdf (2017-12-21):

ITEM NO. | PART NUMBER | DESCRIPTION | QTY.
1 | Base | | 1

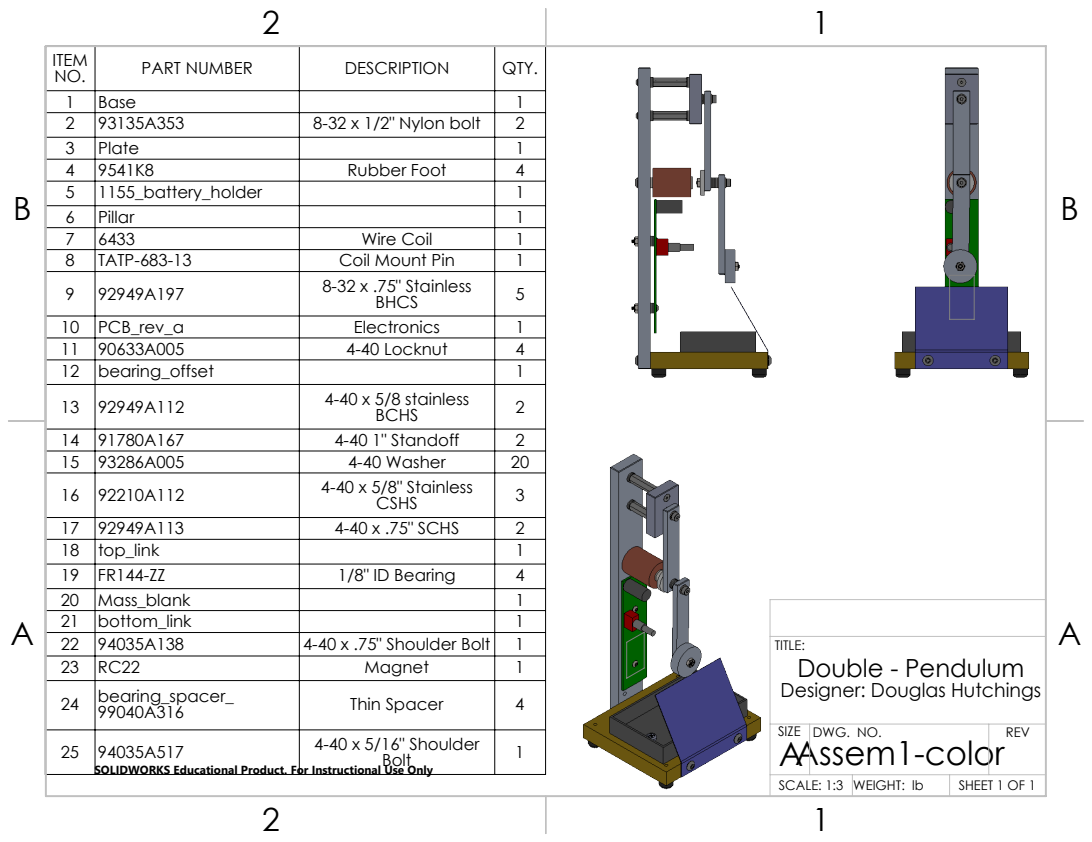
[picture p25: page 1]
TITLE:

2 | 93135A353 | 8-32 x 1/2" Nylon bolt | 2
3 | Plate | | 1
4 | 9541K8 | Rubber Foot | 4
5 | 1155_battery_holder | | 1
6 | Pillar | | 1
7 | 6433 | Wire Coil | 1
8 | TATP-683-13 | Coil Mount Pin | 1
9 | 92949A197 | 8-32 x .75" Stainless BHCS | 5
10 | PCB_rev_a | Electronics | 1
11 | 90633A005 | 4-40 Locknut | 4
12 | bearing_offset | | 1
13 | 92949A112 | 4-40 x 5/8 stainless BCHS | 2
14 | 91780A167 | 4-40 1" Standoff | 2
15 | 93286A005 | 4-40 Washer | 20
16 | 92210A112 | 4-40 x 5/8" Stainless CSHS | 3
17 | 92949A113 | 4-40 x .75" SCHS | 2
18 | top_link | | 1
19 | FR144-ZZ | 1/8" ID Bearing | 4
20 | Mass_blank | | 1
21 | bottom_link | | 1
22 | 94035A138 | 4-40 x .75" Shoulder Bolt | 1
23 | RC22 | Magnet | 1
24 | bearing_spacer_ 99040A316 | Thin Spacer | 4

Double - Pendulum
Designer: Douglas Hutchings

SIZE A Assem1-color | DWG. NO. | REV

25 | 94035A517 SOLIDWORKS Educational Product. For Instructional Use Only | 4-40 x 5/16" Shoulder Bolt | 1

SCALE: 1:3 | WEIGHT: lb | SHEET 1 OF 1

ITEM NO. | PART NUMBER | DESCRIPTION | QTY.
1 | Base_assy | | 1

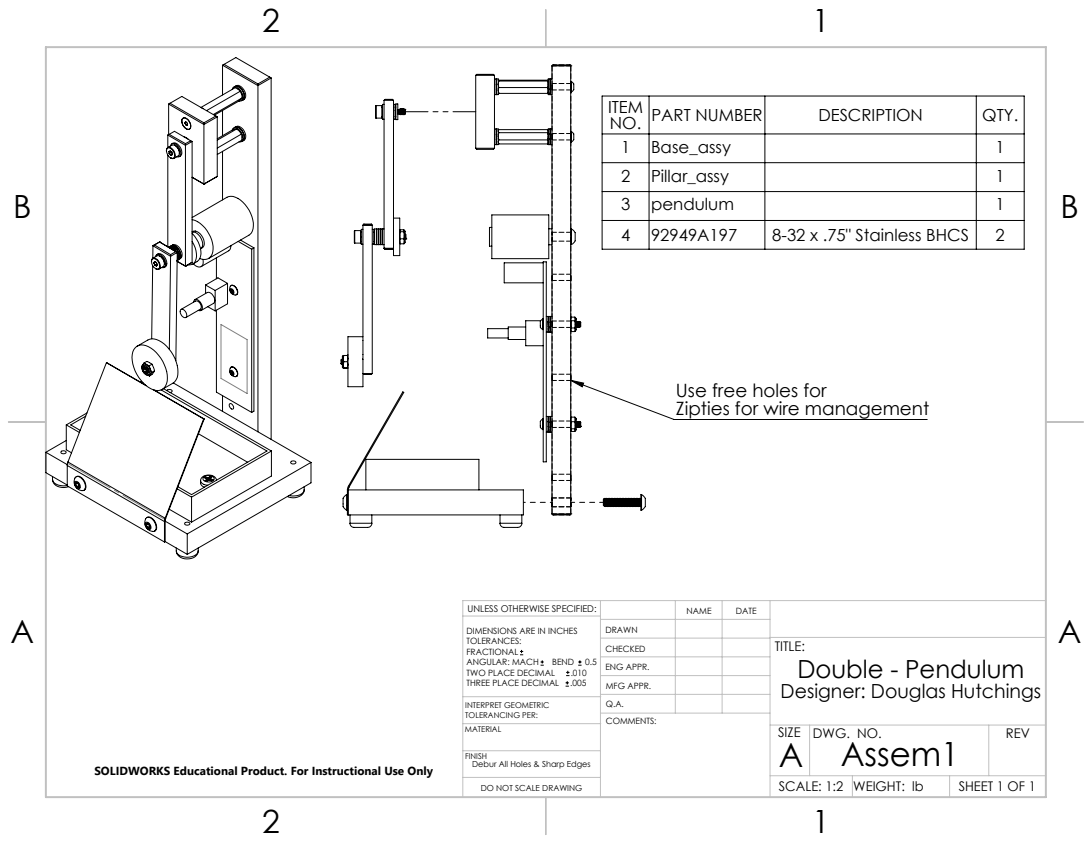
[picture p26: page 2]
Assem1; SHEET 1 OF 1; SCALE: 1:2; WEIGHT: lb; DWG. NO.; REV; SIZE; COMMENTS:; FINISH; MATERIAL

2 | Pillar_assy | | 1
3 | pendulum | | 1
4 | 92949A197 | 8-32 x .75" Stainless BHCS | 2

Use free holes for
Zipties for wire management

UNLESS OTHERWISE SPECIFIED: | | NAME | DATE
DIMENSIONS ARE IN INCHES TOLERANCES: FRACTIONAL ANGULAR: MACH BEND 0.5 TWO PLACE DECIMAL .010 THREE PLACE DECIMAL .005 | DRAWN

CHECKED | | | TITLE: Double - Pendulum Designer: Douglas Hutchings

ENG APPR.
MFG APPR.

INTERPRET GEOMETRIC TOLERANCING PER: | Q.A.

Debur All Holes & Sharp Edges SOLIDWORKS Educational Product. For Instructional Use Only

DO NOT SCALE DRAWING

# 2x 8-32 UNC #29 (.136) drill

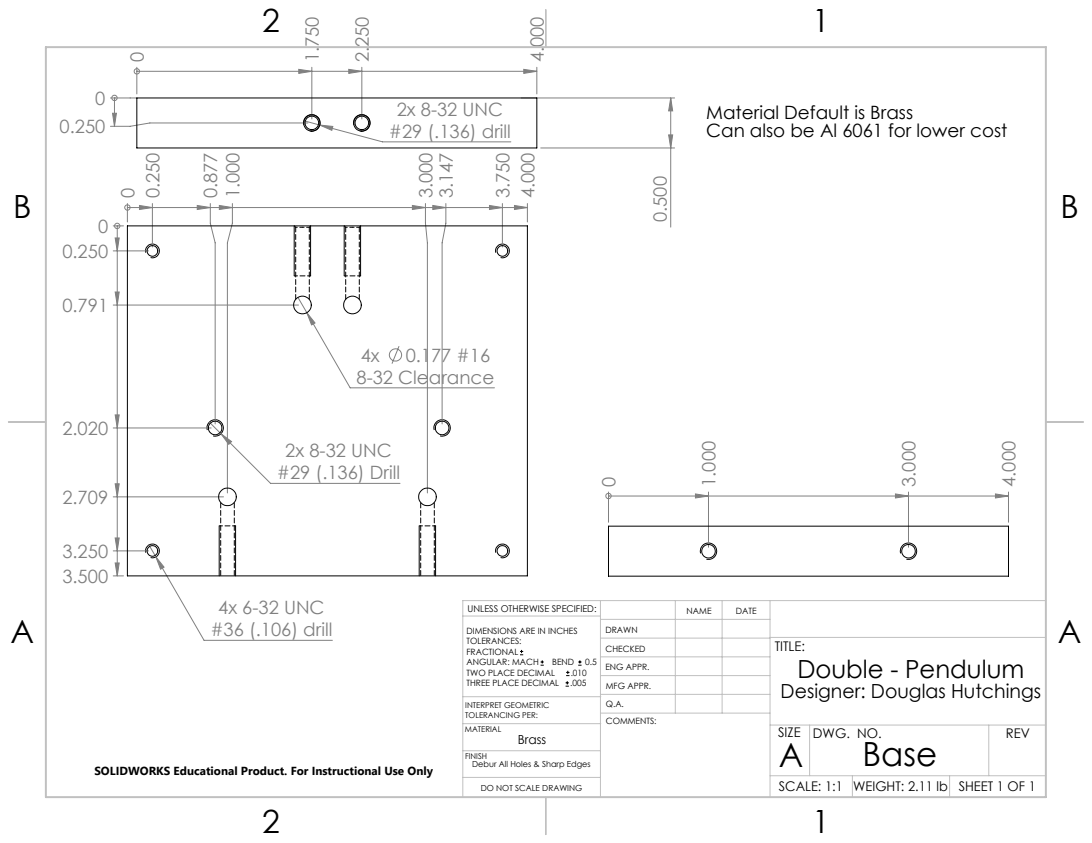
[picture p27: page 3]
4x 6-32 UNC #36 (.106) drill; 4x 0.177 #16 8-32 Clearance; 2x 8-32 UNC #29 (.136) Drill; Brass; Base; SCALE: 1:1; WEIGHT: 2.11 lb; DWG. NO.; REV; SIZE; COMMENTS:; FINISH; MATERIAL

Material Default is Brass
Can also be Al 6061 for lower cost

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

CHECKED | | | TITLE: Double - Pendulum Designer: Douglas Hutchings

ENG APPR.
MFG APPR.

INTERPRET GEOMETRIC TOLERANCING PER: | Q.A.

Debur All Holes & Sharp Edges SOLIDWORKS Educational Product. For Instructional Use Only

B | B

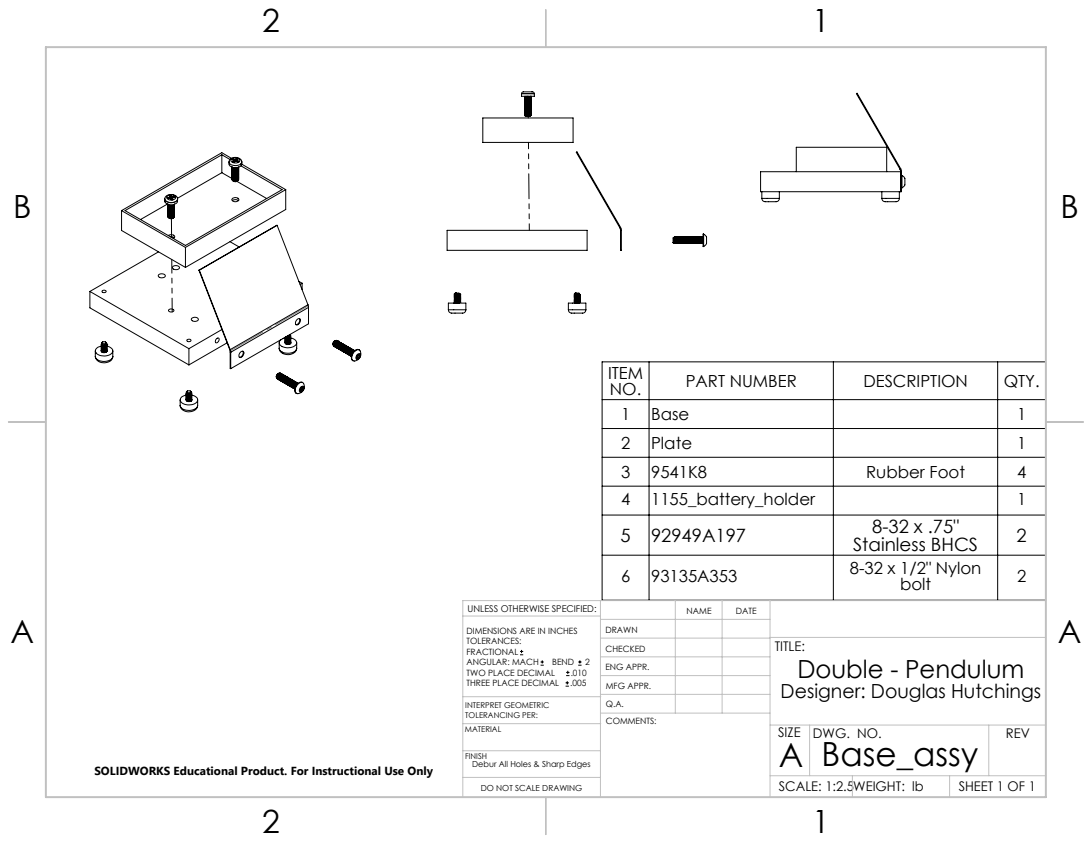
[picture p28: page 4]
Base_assy; SCALE: 1:2.5WEIGHT: lb; DWG. NO.; REV; SIZE; COMMENTS:; FINISH; MATERIAL

ITEM NO. | PART NUMBER | DESCRIPTION | QTY.
1 | Base | | 1
2 | Plate | | 1
3 | 9541K8 | Rubber Foot | 4
4 | 1155_battery_holder | | 1
5 | 92949A197 | 8-32 x .75" Stainless BHCS | 2
6 | 93135A353 | 8-32 x 1/2" Nylon bolt | 2

UNLESS OTHERWISE SPECIFIED: | | NAME | DATE
DIMENSIONS ARE IN INCHES TOLERANCES: FRACTIONAL ANGULAR: MACH BEND 2 TWO PLACE DECIMAL .010 THREE PLACE DECIMAL .005 | DRAWN

CHECKED | | | TITLE: Double - Pendulum Designer: Douglas Hutchings

ENG APPR.
MFG APPR.

INTERPRET GEOMETRIC TOLERANCING PER: | Q.A.

Debur All Holes & Sharp Edges SOLIDWORKS Educational Product. For Instructional Use Only

# 2x 0.129 #30 Drill #4-40 Clearance

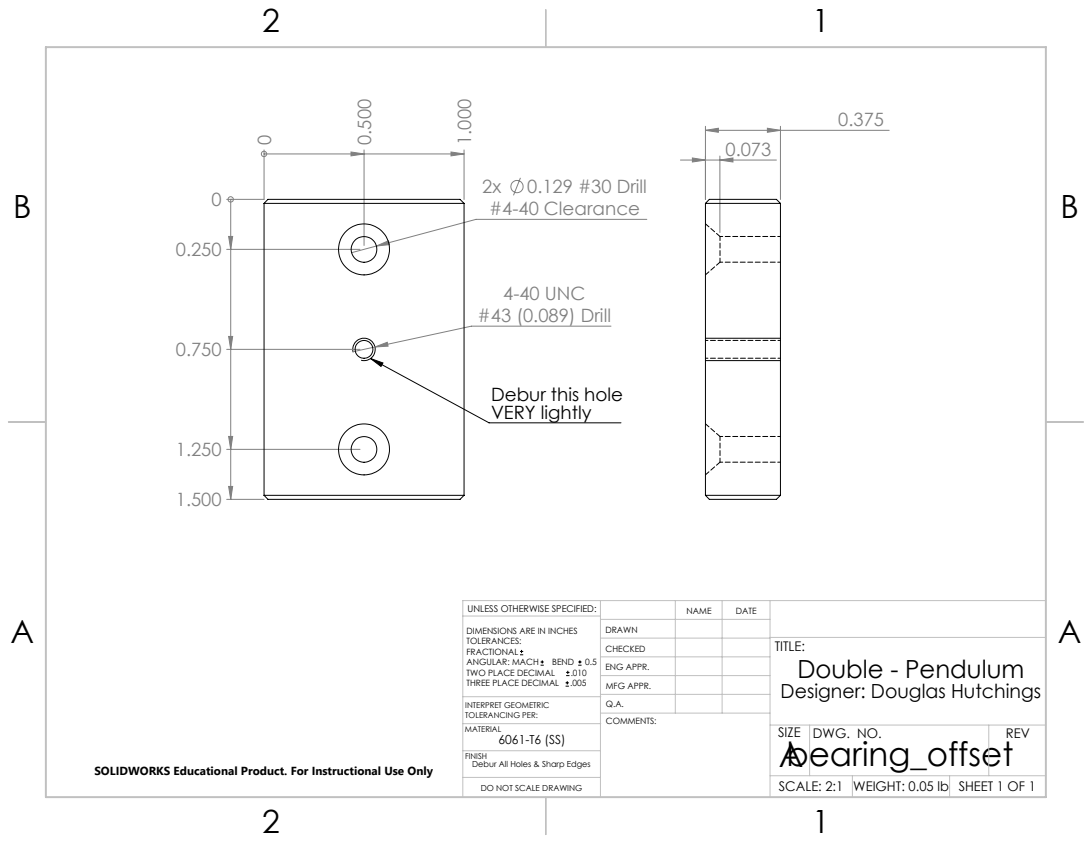
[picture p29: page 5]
4-40 UNC #43 (0.089) Drill; bearing_offset; SCALE: 2:1; WEIGHT: 0.05 lb; DWG. NO.; REV; SIZE; COMMENTS:; FINISH; MATERIAL

Debur this hole
VERY lightly

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

CHECKED | | | TITLE: Double - Pendulum Designer: Douglas Hutchings

ENG APPR.
MFG APPR.

INTERPRET GEOMETRIC TOLERANCING PER: | Q.A.

Debur All Holes & Sharp Edges SOLIDWORKS Educational Product. For Instructional Use Only

B | B

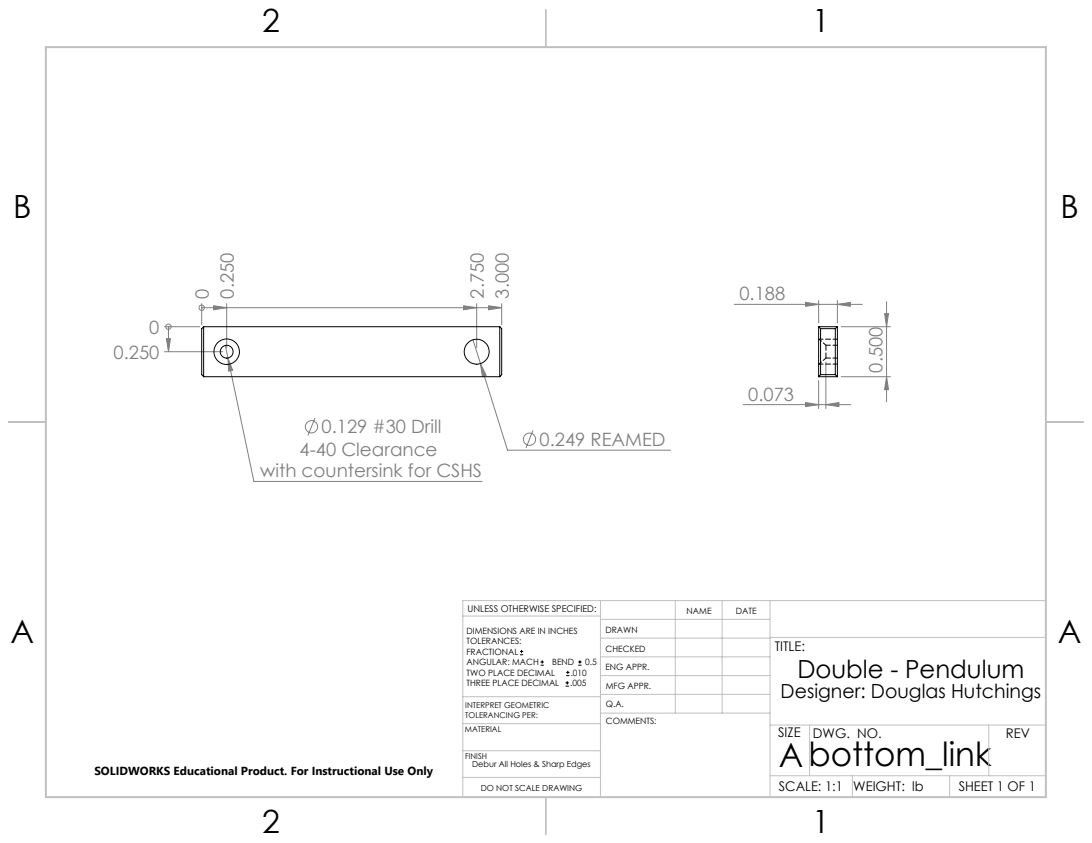
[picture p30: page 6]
0.249 REAMED; bottom_link; SCALE: 1:1; WEIGHT: lb; DWG. NO.; REV; SIZE; COMMENTS:; FINISH; MATERIAL

0.129 #30 Drill
4-40 Clearance
with countersink for CSHS

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

CHECKED | | | TITLE: Double - Pendulum Designer: Douglas Hutchings

ENG APPR.
MFG APPR.

INTERPRET GEOMETRIC TOLERANCING PER: | Q.A.

Debur All Holes & Sharp Edges SOLIDWORKS Educational Product. For Instructional Use Only
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

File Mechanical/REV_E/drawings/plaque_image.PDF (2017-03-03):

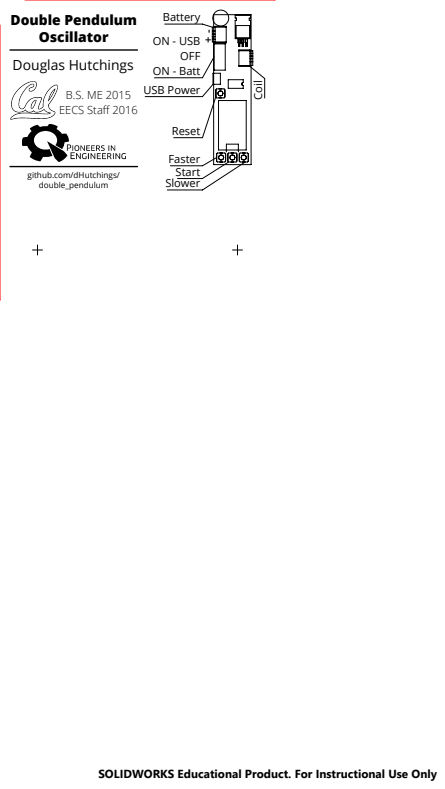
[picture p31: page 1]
USB Power; ON - USB; ON - Batt; Double Pendulum; Douglas Hutchings; B.S. ME 2015 EECS Staff 2016

github.com/dHutchings/
double_pendulum

SOLIDWORKS Educational Product. For Instructional Use Only

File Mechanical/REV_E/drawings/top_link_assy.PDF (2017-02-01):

Pressfit Bearings; SHEET 1 OF 1; SCALE: 1:1; WEIGHT: lb; DWG. NO.; REV

ITEM NO. | PART NUMBER | DESCRIPTION | QTY.
1 | top_link | | 1
2 | FR144-ZZ | 1/8" ID Bearing | 2

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

CHECKED | | | TITLE: Double - Pendulum Designer: Douglas Hutchings

ENG APPR.
MFG APPR.

INTERPRET GEOMETRIC TOLERANCING PER: | Q.A.

Debur All Holes & Sharp Edges SOLIDWORKS Educational Product. For Instructional Use Only

DO NOT SCALE DRAWING


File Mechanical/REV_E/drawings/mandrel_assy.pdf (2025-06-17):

SECTION A-A; SCALE: 2:1; Weight:; SHEET 1 OF 1; DWG. NO.; REV; INTERPRET GEOMETRIC TOLERANCING PER:

ITEM NO. | PART NUMBER | DESCRIPTION | QTY.
1 | winding_mandrel_ma chined | | 1
2 | electromagnet | | 1
3 | 92949A197 | 18-8 Stainless Steel Button Head Hex Drive Screw | 1

3/4" long, head sanded to fit

UNLESS OTHERWISE SPECIFIED:

DRAWING FILE LOCATION

C:\Users\squishy-
2\Desktop\double_pendulum\Mechanical\REV_E\tools\
mandrel_assy.slddrw

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

PART FILE LOCATION

mandrel_assy

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

DO NOT SCALE DRAWING

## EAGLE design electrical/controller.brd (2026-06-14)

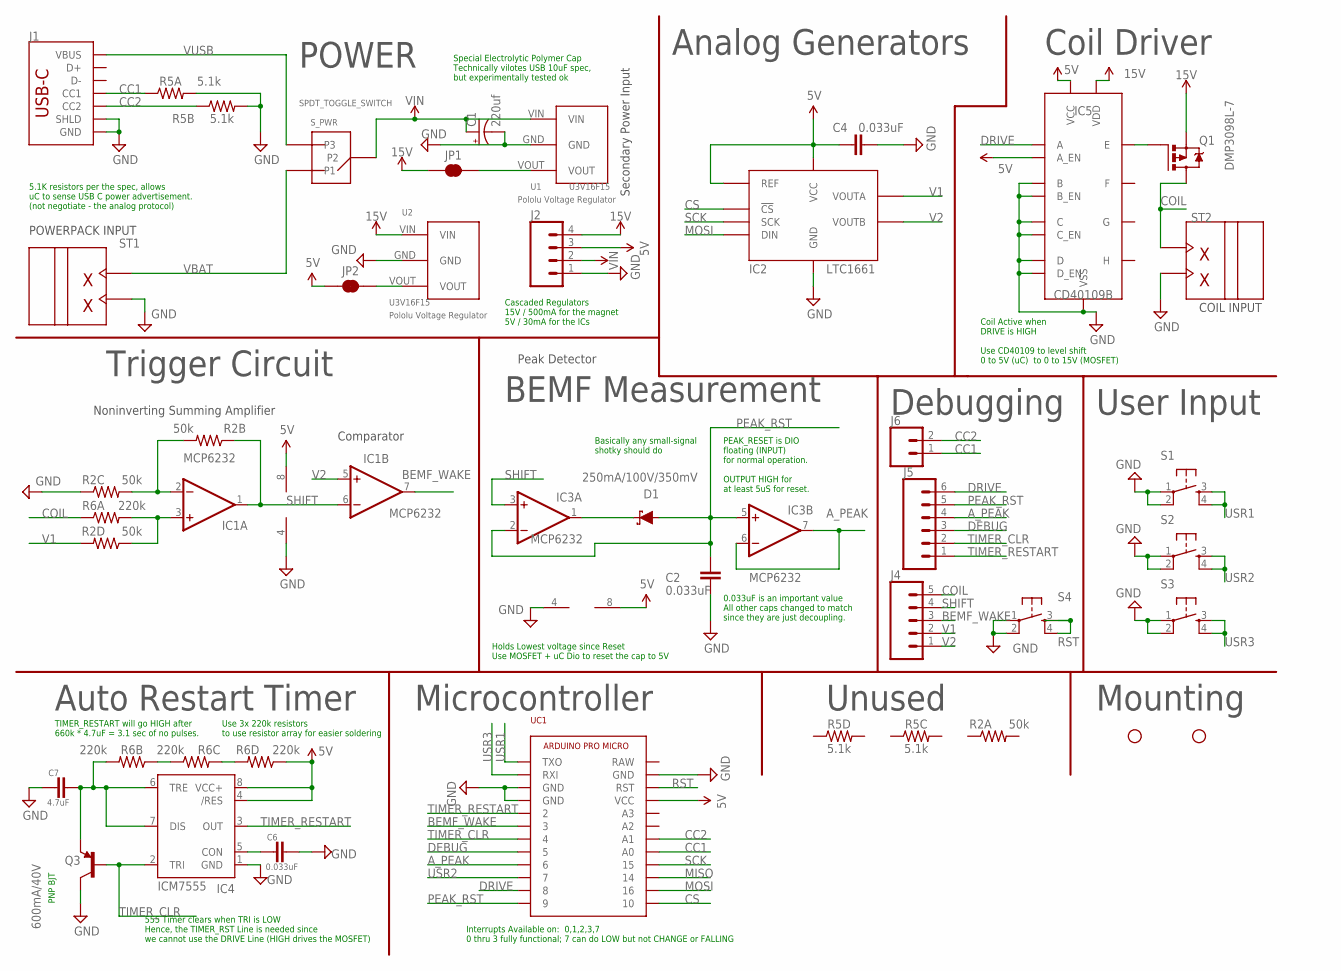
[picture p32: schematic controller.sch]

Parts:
C1: 220uf; E2,5-7
C2, C4, C6: 0.033uF; 0603-CAP
C7: 4.7uF; 0603-CAP
D1: 250mA/100V/350mV; SOD-323
IC1, IC3: MCP6232; SO08
IC2: LTC1661MSOP8; SOP65P490X110-8N
IC4: ICM7555; SO08
IC5: CD40109B; SOP65P640X120-16N
J1: USB_C_2-LAYER_PADS; USB-C-16P-2LAYER-PADS
J2: CONN_041X04_NO_SILK; 1X04_NO_SILK
J4: CONN_05NO_SILK; 1X05_NO_SILK
J5: CONN_06NO_SILK_NO_POP; 1X06_NO_SILK
J6: CONN_021X02_NO_SILK; 1X02_NO_SILK
JP1, JP2: JUMPER-SMT_2_NC_TRACE_SILK; SMT-JUMPER_2_NC_TRACE_SILK
Q1: DMP3098; SOT23-3
Q3: 600mA/40V; SOT23-3
R2: 50k; 1206_RA
R5: 5.1k; 1206_RA
R6: 220k; 1206_RA
S1, S2, S3, S4: TAC_SWITCHPTH; TACTILE-PTH
ST1, ST2: 2PIN_SCREW
STANDOFF1, STANDOFF2: STAND-OFFKEYSTONE_SMT_STANDOFF; KEYSTONE-4881
S_PWR: SPDT_TOGGLE_SWITCH; E-SWITCH-SPDT
U1: U3V16F15; POLOLU_VOLTAG_REGULATOR_U3V16FX_VERT
U2: U3V16F15; POLOLU_VOLTAG_REGULATOR_D45V1E1FX_VERT
UC1: ARDUINO_PRO_MICROUSBC; ARDUINO_PRO_MICRO_USBC

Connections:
5V: C4.1, IC1.8 (V+), IC2.4 (REF), IC2.6 (VCC), IC3.8 (V+), IC4.4 (/RES), IC4.8 (VCC+), IC5.1 (VCC), IC5.2 (A_EN), J2.3, JP2.1, R6.P4 (1), UC1.VCC
15V: IC5.16 (VDD), J2.4, JP1.1, Q1.2 (S), U2.VIN
A_PEAK: IC3.6 (-IN), IC3.7 (OUT), J5.4, UC1.6
BEMF_WAKE: IC1.7 (OUT), J4.3, UC1.3
CC1: J1.A5 (CC1), J6.1, R5.P1 (1), UC1.A0
CC2: J1.B5 (CC2), J6.2, R5.P2 (1), UC1.A1
COIL: J4.5, Q1.3 (D), R6.P1 (1), ST2.P$2
CS: IC2.1 (!CS), UC1.10
DEBUG: J5.3, UC1.5
DRIVE: IC5.3 (A), J5.6, UC1.8
GND: C1.-, C2.2, C4.2, C6.2, C7.1, IC1.4 (V-), IC2.7 (GND), IC3.4 (V-), IC4.1 (GND), IC5.6 (B), IC5.7 (B_EN), IC5.8 (VSS), IC5.9 (C_EN), IC5.10 (C), IC5.14 (D), IC5.15 (D_EN), J1.GND, J1.GND2 (GND), J1.SHLD1 (SHLD), J1.SHLD2 (SHLD), J1.SHLD3 (SHLD), J1.SHLD4 (SHLD), J2.1, Q3.3 (C), R2.P3 (1), R5.P7 (2), R5.P8 (2), S1.1, S1.2, S2.1, S2.2, S3.1, S3.2, S4.1, S4.2, ST1.P$1, ST2.P$1, U1.GND, U2.GND, UC1.GND@0 (GND), UC1.GND@1 (GND), UC1.GND@2 (GND)
MISO: UC1.14
MOSI: IC2.3 (DIN), UC1.16
unnamed: D1.C, IC3.1 (OUT)
unnamed: R6.P2 (1), R6.P3 (1)
unnamed: IC1.3 (+IN), R2.P4 (1), R6.P8 (2)
unnamed: IC1.2 (-IN), R2.P6 (2), R2.P7 (2)
unnamed: C6.1, IC4.5 (CON)
unnamed: C7.2, IC4.6 (TRE), IC4.7 (DIS), Q3.2 (E), R6.P7 (2)
unnamed: JP1.2, U1.VOUT
unnamed: JP2.2, U2.VOUT
unnamed: R6.P5 (2), R6.P6 (2)
unnamed: IC5.4 (E), Q1.1 (G)
PEAK_RST: C2.1, D1.A, IC3.2 (-IN), IC3.5 (+IN), J5.5, UC1.9
RST: S4.3, S4.4, UC1.RST
SCK: IC2.2 (SCK), UC1.15
SHIFT: IC1.1 (OUT), IC1.6 (-IN), IC3.3 (+IN), J4.4, R2.P2 (1)
TIMER_CLR: IC4.2 (TRI), J5.2, Q3.1 (B), UC1.4
TIMER_RESTART: IC4.3 (OUT), J5.1, UC1.2
USR1: S1.3, S1.4, UC1.TXO
USR2: S2.3, S2.4, UC1.7
USR3: S3.3, S3.4, UC1.RXI
V1: IC2.8 (VOUTA), J4.2, R2.P5 (2)
V2: IC1.5 (+IN), IC2.5 (VOUTB), J4.1
VBAT: ST1.P$2, S_PWR.P1
VIN: C1.+, J2.2, S_PWR.P2, U1.VIN
VUSB: J1.VBUS1 (VBUS), J1.VBUS2 (VBUS), S_PWR.P3

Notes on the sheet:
POWERPACK INPUT
Secondary Power Input
COIL INPUT
Trigger Circuit
POWER
Noninverting Summing Amplifier
Comparator
Analog Generators
Debugging
Coil Driver
User Input
Mounting
Interrupts Available on: 0,1,2,3,7 0 thru 3 fully functional; 7 can do LOW but not CHANGE or FALLING
5.1K resistors per the spec, allows uC to sense USB C power advertisement. (not negotiate - the analog protocol)
PNP BJT
DMP3098L-7
Coil Active when DRIVE is HIGH Use CD40109 to level shift 0 to 5V (uC) to 0 to 15V (MOSFET)
555 Timer clears when TRI is LOW Hence, the TIMER_RST Line is needed since we cannot use the DRIVE Line (HIGH drives the MOSFET)
Auto Restart Timer
Microcontroller
BEMF Measurement
Peak Detector
Holds Lowest voltage since Reset Use MOSFET + uC Dio to reset the cap to 5V
Cascaded Regulators 15V / 500mA for the magnet 5V / 30mA for the ICs
TIMER_RESTART will go HIGH after 660k * 4.7uF = 3.1 sec of no pulses.
PEAK_RESET is DIO floating (INPUT) for normal operation. OUTPUT HIGH for at least 5uS for reset.
0.033uF is an important value All other caps changed to match since they are just decoupling.
Basically any small-signal shotky should do
Use 3x 220k resistors to use resistor array for easier soldering
Unused
Special Electrolytic Polymer Cap Technically vilotes USB 10uF spec, but experimentally tested ok

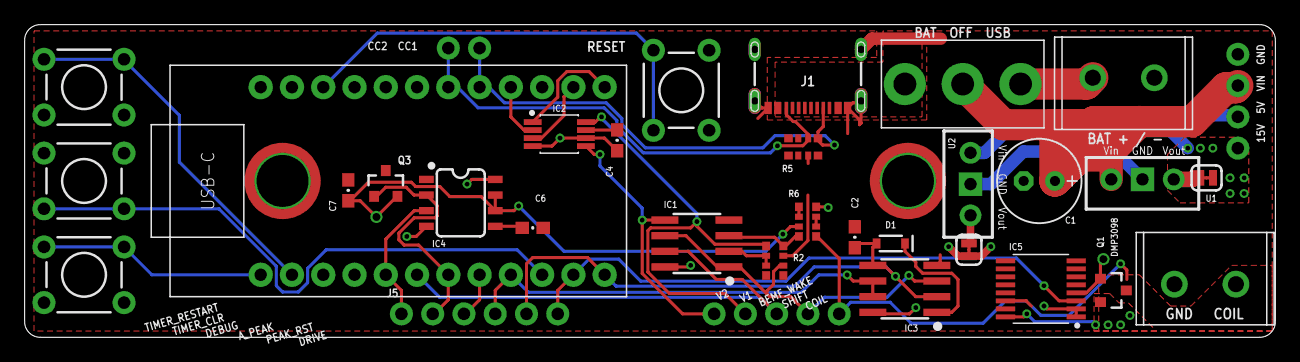
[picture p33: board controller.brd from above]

Board: 2 copper layers, 101.6 x 25.4 mm, 35 parts (0 on the bottom side), 36 nets.

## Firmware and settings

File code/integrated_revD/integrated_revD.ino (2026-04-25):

#include <LowPower.h> //https://github.com/LowPowerLab/LowPower //LowPower_LowPower on the library manager
#include <TimerOne.h>

#include "pins.h"
#include "constants.h"


extern long final_time;

enum POWERUP_REASONS {
  PUSH,
  AUTO_RESTART,
  MANUAL_RESTART,
  UI,
  DEEPSLEEP_WAIT, //This uses the powerDown mode
  LIGHTSLEEP_WAIT, //This uses the powerStandby mode
};

int REASON_FOR_POWERUP = DEEPSLEEP_WAIT; //a nice, neutral, way to start

void setup() {

  #if DEBUG_PRINTS
  Serial.begin(115200);
  delay(5000);
  Serial.println("Hello World");
  delay(1000);

    #if DEBUG
    Serial.println("Warning: DEBUG prints will interfere with the TX LED (the one on the left, as the USB is pointed down");
    #endif

  #else
  //various powersaving which trims 29uA off the power consumption, Praise be to https://forum.arduino.cc/t/power-consumption-of-atmega32u4-during-sleep-power-down-higher-than-expected/685915/28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
  //these probably kill serial prints, so only run them if we need the debug prints.
  USBCON |= (1 << FRZCLK);             // Freeze the USB Clock              
  PLLCSR &= ~(1 << PLLE);              // Disable the USB Clock (PPL) 
  USBCON &=  ~(1 << USBE  );           // Disable the USB  
  #endif


  setup_driver();
  setup_dac();
  setup_ui();
  load_from_eeprom();
  start_pendulum();
  NUM_RESTARTS_SINCE_UI_CHANGE = 0;
  setup_zero_crossing_sensing(); //do this after the pendulum is started so we dont worry about any "triggering the drive" interrupt problems.
  setup_BEMF_sensing(); 
  #if USE_RESTART
  setup_restart(); //do this AFTER the pendulum is started so we can clear the timer...
  #endif

  
}

void loop() {
  #if MOD_DEBUG_PRINTS
  if( (REASON_FOR_POWERUP != DEEPSLEEP_WAIT) && (REASON_FOR_POWERUP != LIGHTSLEEP_WAIT)) //in debug mode, we do a lot of DEEP_SLEEP waits that fill the screen (actually, 1ms delay)
  //we don't want to see those.
  {
    Serial.print("Powerup: ");
    Serial.println(REASON_FOR_POWERUP);    
  }
  #endif

  switch(REASON_FOR_POWERUP)
  {
    
    case PUSH:
      //detachInterrupt before doing the starting, so we don't have the secondary flyback pulses interrupt our handing of this.
      detachInterrupt(digitalPinToInterrupt(bemf_wake));

      
      push();

      #if USE_POST_PUSH_TIMEOUT
        powerStandby_allowPrints(SLEEP_TIMEOUT);
      #endif
      
      //attach interrupts again.
      setup_zero_crossing_sensing();

      #if COUNT_PRINTS
      Serial.print("Num Pushes: ");
      Serial.print(NUM_PUSHES_BETWEEN_RESTARTS);
      Serial.print("\t Num Restarts: ");
      Serial.println(NUM_RESTARTS_SINCE_UI_CHANGE);      
      #endif

      
      REASON_FOR_POWERUP = DEEPSLEEP_WAIT;
      break;
    case AUTO_RESTART:
      //detachInterrupt before doing the starting, so we can start cleanly w/out the startup sequence.
      detachInterrupt(digitalPinToInterrupt(auto_timer_restart)); //i tried falling, but because TIMER_RESTART is bound to Dio 7 right now, Falling doesn't work and I have to rely on LOW.
      detachInterrupt(digitalPinToInterrupt(bemf_wake));
      
      //Don't need to detach reattach interrupts - all the interrupt does is change a flag now (which I will shortly change, down here)
      start_pendulum();


    
      #if USE_POST_PUSH_TIMEOUT
        powerStandby_allowPrints(SLEEP_TIMEOUT);
      #endif

      //attach interrupts again.
      #if USE_RESTART
      setup_restart_interrupt();
      #endif
      setup_zero_crossing_sensing();


      REASON_FOR_POWERUP = DEEPSLEEP_WAIT;
      break;
    case MANUAL_RESTART:
      detachInterrupt(digitalPinToInterrupt(auto_timer_restart));
      detachInterrupt(digitalPinToInterrupt(bemf_wake));
      start_pendulum();

      #if USE_POST_PUSH_TIMEOUT
      powerStandby_allowPrints(SLEEP_TIMEOUT);
      #endif

      //attach interrupts again.
      #if USE_RESTART
      setup_restart_interrupt();
      #endif
      setup_zero_crossing_sensing();

      break;
    case UI:
      NUM_RESTARTS_SINCE_UI_CHANGE = 0; //reset a helpful debug counter.
      REASON_FOR_POWERUP = DEEPSLEEP_WAIT;
      break; //do nothing, the UI interrupt handlers dealt with it
    case DEEPSLEEP_WAIT:
      break;
    case LIGHTSLEEP_WAIT:
      break;    
  }

  //depending on the sleep mode, do different things here.
  if(REASON_FOR_POWERUP == DEEPSLEEP_WAIT)
  {
    #if (!DEBUG_PRINTS)
    LowPower.powerDown(SLEEP_FOREVER,ADC_OFF,BOD_ON); //70 uA-ish --> See the power tester for more info.
    #else
    delay(1);//need some timing room for the debug prints to come through.  This is far, far, far more reliable for whatever reason than powerStandby_allowPrints(SLEEP_FOREVER);
    #endif
  }
  else if(REASON_FOR_POWERUP == LIGHTSLEEP_WAIT)  //This specific condition may interf
  {
    #if (!DEBUG_PRINTS)
    //500 uA-ish --> See the power tester for more info.  but only on pins 2&3.  0&1 draw ~.5mA.    
    //powerStandby wakes up much faster than powerDown, likely because powerStandby keeps the crystal oscilator running (https://www.engineersgarage.com/reducing-arduino-power-consumption-sleep-modes/)
    powerStandby_allowPrints(SLEEP_FOREVER);
    #else
    delay(1);//need some timing room for the debug prints to come through.  This is far, far, far more reliable for whatever reason than powerStandby_allowPrints(SLEEP_FOREVER);
    #endif
  }
  
}

void blank_ISR()
{
  
}

void powerStandby_allowPrints(period_t timeout) //power standby  - the lowest power saving mode (which breaks prints)- but...
//pay attention to the #define flags so if prints are needed; use the lesser precise_idle which allows prints through.
{
  
  #if !DEBUG_PRINTS
  LowPower.powerStandby(timeout,ADC_OFF,BOD_ON); //can only do this if I'm not printing.
  #else //If I am printing, I have to let the print go through so I have to use a lesser timeout.

  switch(timeout)
  {
    case SLEEP_15MS:
      precise_idle(15000);
      break;
    case SLEEP_30MS:
      precise_idle(30000);
      break;
    case SLEEP_60MS:
      precise_idle(60000);
      break;
    case SLEEP_120MS:
      precise_idle(120000);
      break;
    case SLEEP_250MS:
      precise_idle(250000);
      break;
    case SLEEP_500MS:
      precise_idle(500000);
      break;
    case SLEEP_1S:
      precise_idle(1000000);
      break;
    case SLEEP_2S:
      precise_idle(2000000);
      break;
    case SLEEP_4S:
      precise_idle(4000000);
      break;
    case SLEEP_8S:
      precise_idle(8000000);   
      break;
    case SLEEP_FOREVER:
      precise_idle(1000); //not actually forever, 1ms.  then let the loop keep running   
      break;
  }
  #endif
}

void precise_idle(long tim) //allow ability to delay up to 8.3 seconds highly precisely while in IDLE (17mA) - a power saving mode, but not the most aggressive.
{
  if(tim <= 0)
  {
    return;
  }
  //delayMicroseconds(tim);
  //return;
  
  Timer1.initialize(tim);
  Timer1.attachInterrupt(blank_ISR); //have to attach an interrupt to a blank function, otherwise, it wont generate an interrupt that will get us out of idle.
  LowPower.idle(SLEEP_FOREVER, ADC_OFF, TIMER4_OFF, TIMER3_OFF, TIMER1_ON, TIMER0_OFF, SPI_OFF, USART1_OFF, TWI_OFF, USB_OFF); //About 17.1 mA
  Timer1.stop();  

}
void delay_many_microseconds(unsigned long tim) //allow ability to delay more than 16.3k uS... this does not have any power saving modes.
{
  unsigned long time_left = tim;

  while(time_left > 0)
  {
    if(time_left > 16000)
    {
      delayMicroseconds(16000);
      time_left = time_left - 16000;
    }
    else
    {
      delayMicroseconds(int(time_left));
      time_left = 0;
    }
    
  }
  
}

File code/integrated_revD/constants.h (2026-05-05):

#ifndef CONSTANTS_H
#define CONSTANTS_H


/* Kinematics Constants: PUSH TIME  */
static long NOMINAL_PUSH = 7750; //nominal push time, fixed value that we always use.
static long MAX_PUSH = 25000;
static long MIN_PUSH = 500;
static long PUSH_SETTING_STEP = 250;

volatile long push_time_us = NOMINAL_PUSH;  //actual push time.  It needs to be here, since multiple code segments deal with it.  Can be adjusted up and down via button presses

/* pump more energy into the pendulum just after a restart */
long RESTART_EXTRA_PUSH_AMOUNT = 4000; //extra amount to push after I just restarted.
int RESTART_EXTA_PURHSES_COUNT = 30; //at a decreasing amount for these number of pushes.

/* and RANDOMNESS so we can break out of limit cycles */
volatile long RANDOM_AMOUNT = 2000; //allow for +/- 2000uS push time randomness... used to prevent long-term cyclic oscilations.  Same as the 40% of the push time it was in rev C
volatile long random_time; //random value, can have a negative value so not unsigned.  This is actually the dyamically computed random value

#define SCALE_RANDOMNESS true //set to true to enable the amount of randomness to be scaled up and down by how much we are over or underpushing, not just some nominal value.
//the real random push time will be scaled up or down from this value.  EG the nominal push time is 5500uS.  If it's half of that (2750 uS), the nominal random time max could cause a negative push time.

#define OUTSTRECHED_ARM_DETECTION true //set to true to enable BEMF sensing noticing that the pendulum is too fast to temporarily suspend pushes
#define OUTSTRECHED_ARM_SLOWING false //set to true to enable BEMF sensing noticing that the pendulum is too fast to slow down the push speed

volatile int MAX_PUSHES = 3; //number of times the pendulum will push untill is chooses a new random push time
volatile int CHANCE_NO_PUSH = 5; //10% chance of not pushing this time, b/c randomness.  Set to -1 to turn off.



#define USE_POST_PUSH_TIMEOUT true //set to true to enable a timeout after restarts or pushes - any BEMF triggers in this timeout are ignored.  Cuts down on spurious / power wasting double pushes
period_t SLEEP_TIMEOUT = SLEEP_120MS; //a randomly chosen good number

//Other Stuff

volatile float last_bemf; //the value of the most recent BEMF

volatile int NUM_PUSHES_BETWEEN_RESTARTS = 0;
volatile int NUM_RESTARTS_SINCE_UI_CHANGE = 0;
volatile int NUM_PUSHES_TO_SKIP = 0;

#define DEBUG false //set to true for debug-only TX / RX LEDs.  TX LED (left?) is generally around the drive interrupt trigger times, RX is around the MOSFET driving.

/* DEBUG Print Modes */
#define GENERAL_DEBUG_PRINTS false //set to tue for debug-only prints.  This means the system cannot power down (USB issues).  ALSO, be aware that if the serial monitor window isnt open but we are still trying to send prints, the pendulum will stop working, too.
#define SPEED_DEBUG_PRINTS false //prints to show the BEMF speed.
#define MOD_DEBUG_PRINTS false //wakeup-mode prints.  These things fill the screen
#define COUNT_PRINTS false //set to true to show count of the various pushes / restarts

#define DEBUG_PRINTS false //must be set to the OR of any of the above prints.  If at any one (at least) of the above is true, this must be true too.  ORs aren't working for whatever reason.

/* DEBUG Modes */
#define NO_PUSH false //set to true for absolutely no pushing or driving on the COIL wire.
#define RESET_EEPROM true
#define USE_RESTART true

/* Curve Threshold Sensing Offsets */
float voltage_add = 1.2;  //Shift the voltage curve measured from the coil of wire up by 2 volts.  We set the V1 to be 1.2V and the op-amp resistor feedback network will scale the COIL and shift it up by 2.
float voltage_threshold = 1.65;  //Set the threshold to generate an trigger for the interrupt in to 1.65 volts.  Therefore, the voltage cuve must be -.35V to change the comparator's output.  The interrumpt will be generated low-to-high just before the zero point.


#endif

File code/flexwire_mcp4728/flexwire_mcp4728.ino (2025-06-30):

// Basic demo for configuring the MCP4728 4-Channel 12-bit I2C DAC
#include "Wire.h"


int SCL_line = 8;
int SDA_line = 6;
FlexWire Wire = FlexWire(SDA_line, SCL_line);

#include <Adafruit_MCP4728.h>

Adafruit_MCP4728 mcp = Adafruit_MCP4728();

void setup(void) {
  Serial.begin(115200);
  while (!Serial)
    delay(10); // will pause Zero, Leonardo, etc until serial console opens

  Serial.println("Adafruit MCP4728 test!");

  // Try to initialize!
  if (!mcp.begin()) {
    Serial.println("Failed to find MCP4728 chip");
    while (1) {
      delay(10);
    }
  }

  mcp.setChannelValue(MCP4728_CHANNEL_A, 4095);  //using external VREF, maximum value
  mcp.setChannelValue(MCP4728_CHANNEL_B, 2048, MCP4728_VREF_INTERNAL, MCP4728_GAIN_1X); //using the internal Vref (2.048V) set to 1/2 of the full 12-bit value, so should be 1.024V.

  //Turn the other channels off, according to the datasheet this saves 400 uA and is the only reason this chip consumes less power than the older 1 channel DACs
  mcp.setChannelValue(MCP4728_CHANNEL_C, 0,MCP4728_VREF_INTERNAL, MCP4728_GAIN_1X,MCP4728_PD_MODE_GND_500K);
  mcp.setChannelValue(MCP4728_CHANNEL_D, 0,MCP4728_VREF_INTERNAL, MCP4728_GAIN_1X,MCP4728_PD_MODE_GND_500K);
}

void loop() { delay(1000); }

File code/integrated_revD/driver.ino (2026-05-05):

#include "constants.h"


//purely internal variables
volatile int prev_pushes; //how many times have I pushed since I last chose a random number?
long final_time; //how long I plan to push on the next push.  Leave it here so others can get it.

void setup_driver()
{
  #if !NO_PUSH //if we aren't pushing, don't even bother setting it as an output.  
  pinMode(drive_mosfet,OUTPUT);
  #endif
  drive_MOS(LOW);
  delay(100); //just in case transients from MOSFET.

}

void  setup_zero_crossing_sensing()
{
  
  pinMode(bemf_wake,INPUT_PULLUP);
  attachInterrupt(digitalPinToInterrupt(bemf_wake),interrupt_wake,CHANGE);

}

void interrupt_wake() //the helper that triggers the wake (either if I'm in deep, or light sleep).  It will figure out what the correct next step is based on the sign of the INT pin
{
  if(digitalRead(bemf_wake)) //this is a RISING edge.  That's the first edge I get.  I don't want to do anyting here.
  {
    #if DEBUG
    digitalWrite(LED_BUILTIN_TX, LOW); // Turn TX LED on  
    #endif

   REASON_FOR_POWERUP = LIGHTSLEEP_WAIT;
  }
  else
  {
    #if DEBUG
    digitalWrite(LED_BUILTIN_TX, HIGH); // Turn TX LED off  
    #endif

    REASON_FOR_POWERUP = PUSH;
  }
}


void push()
{
  NUM_PUSHES_BETWEEN_RESTARTS += 1; //keep track of the number of pushes between restarts.
  #if DEBUG
  digitalWrite(LED_BUILTIN_RX, LOW); // Turn RX LED on
  #endif

  last_bemf = measure_BEMF(); //do this first, so I know how fast we're going, before A) I decide to skip this push or B) Flyback is picked up by the negative peak detector and I get a phony value

  #if SCALE_RANDOMNESS
  if( (random(0,100) < CHANCE_NO_PUSH) && (NUM_PUSHES_BETWEEN_RESTARTS > RESTART_EXTA_PURHSES_COUNT))  //sometimes, don't push.  BUT, don't not push untill I have fully started starting up and have gotten through all the larger pushes.
  #else
  if(random(0,100) < CHANCE_NO_PUSH)  //sometimes, don't push.
  #endif
  {
    NUM_PUSHES_TO_SKIP += 1;
  }
  
  if(NUM_PUSHES_TO_SKIP == 0)
  {
    long estimated_time_to_center_pulse = peak_time_us_after_INT(last_bemf); 
    final_time = push_time_us + random_time;

    //Center the pulse in time at the expected BEMF POSITIVE peak based on the negative BEMF measurement and the idea that the BEMF pulse should be relatively symmetric..
    
    precise_idle( (estimated_time_to_center_pulse) - (final_time/2) - 2100); //wait untill it's the exact right time to turn on the pulse.

    //the 21 is DEFINATELY a hack - it's probably the system overhead from the code running + the interrupt waking things up.
    //but per an o-scope that's the time I need to shift the calculated curve by to get it to the right place (peak BEMF in the middle).
    //I'm not able to nail the timing 100% consistently, but, the overall concept of "push at a more optimum time" really does seem to work.
    //Clearly, BEMF sensing + interrupt timing + wake up timing isn't as good as a hall sensor to trigger the switch.

      
    //delayMicroseconds(1); //allow to cross zero.
    //this delay, is really should be on the order of MS, if we even use it!
    //This new (lower current, but slower) op-amps slew rate is so dang long that using the op-amp as a comparator is easy, but, may be bad.  We may want to go faster.
    //left in for future-proofing, but i may not need this.  uC requires significant time to wake from powerOff state, and I can change timing by also affecting the voltage threshold value.

    //If I started recently, push harder.    
    if( NUM_PUSHES_BETWEEN_RESTARTS <= RESTART_EXTA_PURHSES_COUNT)
    {
      /*
      Serial.print(final_time);
      Serial.print("\t");

      Serial.print("Extra %:\t");
      Serial.print(float(RESTART_EXTA_PURHSES_COUNT-NUM_PUSHES_BETWEEN_RESTARTS)/float(RESTART_EXTA_PURHSES_COUNT));
      Serial.print("\t");
      */
      final_time += long(RESTART_EXTRA_PUSH_AMOUNT*float(RESTART_EXTA_PURHSES_COUNT-NUM_PUSHES_BETWEEN_RESTARTS)/float(RESTART_EXTA_PURHSES_COUNT));        
      /*
      Serial.print(final_time);
      Serial.print("\t");
      */
      final_time -= long(random_time/2); //I also want less random time ( <2 is a divide by 2 operation)
      /*
      Serial.print(final_time);
      Serial.print("\t");
      Serial.println();
      */

    }

    drive_MOS(HIGH); //Drive_mosfet HIGH turns the coil on & lets the 555 timer know... we don't care about sign flips here
  
    precise_idle(final_time); //Cuts overall 5V time average from 1.83 ma to 1.572 ma just by precise_idleing here, which cuts in 1/2 the current draw for this very small time.
    //just goes to show how much current the uC draws when fully up.
    //unfortunately, since this time is < 18 ms, I don't think there's a way to save even more power here...
    drive_MOS(LOW);
  
    prev_pushes ++;

    //According to the datasheet (Page 55), the bandgap reference takes 40 to 70uS to start up, and draws 10uA.
    //I havent had any success with saving power via BOD, (fuses?) - while the library's API suggests I can disable BOD
    //on my board its only possible via fuse settings.
    //according to datsheet, BOD on will also put on the Bandgap reference.


    //calculate the NEXT random value.
    if(prev_pushes > MAX_PUSHES)
    {
      prev_pushes = 0;

      #if SCALE_RANDOMNESS
      random_time = long(float(random(-RANDOM_AMOUNT,RANDOM_AMOUNT)) * float(push_time_us) / float(NOMINAL_PUSH)); 
      #else
      random_time = random(-RANDOM_AMOUNT,RANDOM_AMOUNT); 
      #endif
      //scale random time by the nominal max push time
      final_time = push_time_us + random_time;
    }



    #if GENERAL_DEBUG_PRINTS
    Serial.print("Center: ");
    Serial.print(estimated_time_to_center_pulse);
    Serial.print(",\tDelay: ");
    Serial.print(estimated_time_to_center_pulse - final_time/2);
    Serial.print(",\tMed: ");
    Serial.print(push_time_us);
    Serial.print(",\tRand: ");
    Serial.print(random_time);
    Serial.print(",\tPush Time: ");
    Serial.println(final_time);
    #endif
    
  }
  else
  {
    clear_restart_timer(); //I still have to lie to the 555 Reset Timer
    //I noticed that this push should have Occured, I only chose not to this time.
    NUM_PUSHES_TO_SKIP -= 1;
  }


  //do NOT powerStandby_allowPrints(SLEEP_15MS) here.
  //Instead, it is more reliable to finish push() quickly.
  //and then use the extra logic around the REASON_FOR_POWERUP == DEEPSLEEP_WAIT or LIGHTSLEEP_WAIT will take care of that!
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

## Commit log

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2016-12-12 First draft of schematic.
    Routing begins now.
    [controller.brd, controller.sch]
2016-12-12 minor fixes on schematics.
    [controller.brd, controller.sch]
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2016-12-12 Small board fixes
    [controller.brd]
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2016-12-13 Add pre-done Mechanical Files
    Two revs of Solidworks files. New folder for each rev, git doesn't like version controlling binaries.
    [4-40-75-92949A113_.SLDPRT, 4-40-75-92949A113_new.SLDPRT, 4-40_15-32_5-32_94035A134.SLDPRT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]
2016-12-16 New Mechanical Revision
    Rev C:
    Added space for PCB Rev A.
    Added battery holder
    Other minor fixes
    [4-40-75-92949A113_.SLDPRT, 4-40-75-92949A113_new.SLDPRT, 4-40-750-Nylon_93135A278.SLDPRT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]
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2016-12-21 WIP integration
    Things are currently very, very, broken in the electrical realm.
    [DAC.ino]
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2016-12-30 Rev B PCB changes
    New parts, re-route.
    [controller.brd, controller.sch]
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2017-01-03 Update Rev D to fix critical problem
    Self-colliding head.
    [4_40-3-4-94035A138.SLDPRT, bom.csv, pendulum.SLDASM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]
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2017-01-13 Changes to Rev D based on testing
    Re-worked several things about base & plate, such as material choice (brass to make heavier), more tapped holes, etc
    Added holes for zipties to pillar
    added material notes to every drawing & other changes to drawing frames
    added overall BOM w/ color images as another drawing
    Fixed battery holder dimmensions
    [1155_battery_holder.SLDPRT, Assem1.SLDDRW, Base.SLDDRW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]
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2017-01-15 Fixed images on color full assembly drawing
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2017-01-17 Fixed top link drawing
    It now is actually a drawing of the top link assembly.
2017-02-01 Fix Rev B erratta
    Hole sizes for screw terminals
    Pour clearance
    Silkscreen Fixes
    Revision Numbers
    [controller.brd, controller.sch]
2017-02-01 New Docu packet, Bom, and Gerb files for rev C
    [bom.csv]
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2017-03-13 Add restart button
    Middle button can now be used to restart pendulum, w/out changing
    contants. (Start vs Reset)
    [DAC.ino, UI.ino, driver.ino]
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2025-03-26 partial design of new Rev E mechanical design for Spring 2025
    Primary change so far is to drastically A) reduce the number of tapped
    holes reqd on the brass base and B) R&D to make custom electromagnet.
    Minimal changes to plaque and pillar to accomidate.
    So far, no mechanical simplifications done on the pendulum links.
    [1155_battery_holder.SLDPRT, 4-40-75-92949A113_new.SLDPRT, 4_40-1000-HEX STANDOFF_91780A167.SLDPRT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]
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2025-04-07 Various easy-to-make changes to make things look better
    1) internal threading on the massblank - costs us a tap, but looks a lot
    better than a locknut.
    2) Internal threading for the PCB holes - costs us two taps, but looks
    better than the locknuts again
    3) make pillar slightly taller to allow for more clearance due to mass
    blank getting bigger. (9 to 9.25. Pure math says only needs to get
    1/16 bigger, but, it was always tight and buys me room to be a bit
    sloppy on the bending)
    [92805A108_Stainless Steel Thread-Locking Hex Drive Flat Head Screws.SLDPRT, 93310A110_Stainless Steel Thread-Locking Button Head Hex Drive Screws.SLDPRT, Mass_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]
2025-06-17 Finally reasonable progress on the electronics
    This plus github.
    Nearly done fleshing the SCH out.
    Routing should not be difficult, just a few hours.
    Postponing changing the power parts of this circuit untill after the
    spools are done. Everything but the power, I can do now --> ship a
    revision, test it.
    [controller.brd, controller.sch]
2025-06-17 Various mechanical
    Wasnt really bothering to keep mechanical track of things.
    Some model changes for the new batch.
    Also, a bunch of jigs for production.
    [92196A177_18-8 Stainless Steel Socket Head Screw.SLDPRT, 92949A197_18-8 Stainless Steel Button Head Hex Drive Screw.SLDPRT, 92949A199_18-8 Stainless Steel Butt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]
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2025-06-18 Finish rev D1
    Most of hte new features, except without overhauling the power system
    b/c the power system requires tests with spools, which I havent done
    yet.
    [controller.brd, controller.sch]
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2025-06-30 Correct comment on SCH
    Yes, the i2c address is reconfigurable, but hte default is 0x60
    [controller.sch]
2025-07-08 Log Back EMF from legacy electromagnet via O-scope, replicate via DDS Signal Gen
    [clean.csv, ragged.csv]
2025-07-17 Further tweaks to spool 3d printing to finally make the spool winding clean
    [custom_spool.3mf, custom_spool.SLDPRT, custom_spool.STL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]
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2025-07-17 some but not all of the changes for Rev D2
    [controller.brd, controller.sch]
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2025-07-18 Most, but not all, of rev D2
    Still need to test CC1 / CC2.
    Add debug pinout silkscreen labels.
    See if we can still use resistor arrays.
    Calculate new values for the trigger op-amp network.
    [controller.brd, controller.sch]
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2025-07-22 Added resistor arrays + other minor erratta, ready for prod
    [controller.brd, controller.sch]
2025-07-24 Add missing pullup; tweak slots for JLCPCB fab
    [controller.brd, controller.sch]
2025-08-01 Update PCB with short headers; minor pendulum pivot changes
    [1_8_3_16_92510A421_Aluminum Unthreaded Spacer-mod.SLDPRT, 4_40_1-8_90176A102_Nylon Unthreaded Spacers.SLDPRT, 92510A421_Aluminum Unthreaded Spacer.SLDPRT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]
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2025-08-08 Missed some debug prints
    [integrated_revD.ino]
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2025-08-08 POC of BEMF sensing
    POC of both resetting and confirming proper behaviour (via o-scope) AND
    measuring the value via the ADC.
    Could do some things more efficiently, such as that reset, but it does
    work.
    [BEMF.ino, driver.ino, integrated_revD.ino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]
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2025-08-08 Test which pins can do change interrupts and label SCH
    [controller.sch]
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2025-08-08 More correct power down
    [integrated_revD.ino]
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2025-08-09 Add more power, duration tests.
    Turns out that the Low Power library's durations aren't precise -
    they're approximate.
    The only way to do precise powerdowns seems to be by leveraging Timer1 /
    Timer3 calling some interrupt as a way to get us out of the Idle mode.
    Works only for IDLE.
    Thus -->
    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
    [controller.sch]
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2025-08-09 Move push out of ISR into loop; add more power reducing modes
    Keeping all the ISRs short (again, cardinal rule) and moving PUSH and
    RESTART into loop allows us to use the precise idle we developed a few
    commits ago.
    [555_restart.ino, DAC.ino, UI.ino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]
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2025-08-14 Helpful tool for modifying the standoffs for the linkages
    [clamp.3mf, clamp.SLDPRT, clamp.STL]
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2025-08-15 Plop some things onto the PCB, lots of work to do.
    [controller.brd, controller.sch]
2025-08-16 First attempt at routing D3
    Now lets put it in Solidworks and check button accessibility.
    [controller.brd, controller.sch]
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2025-08-16 Various tweaks to mechanical design
    Using those screw nails
    New Rev D3 PCB
    Use shorter shoulder screw + metalic / plastic standoffs to eliminate
    need for stacks of washers.
    [90081A291_Zinc-Plated Steel Screw Nails.SLDPRT, Base.SLDPRT, Base_assy.sldasm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]
2025-10-24 Make prints more stable
    And informative, we get a print each time there's a new push time
    calculated.
    I do think we have an issue with negative push times...
    [driver.ino, integrated_revD.ino]
2025-10-24 Prevent precise idle from running on negative values
    That'd get misinterpreted as huge positive values, effectively freezing
    the system.
    When combined with the randomness, if the randomness was too big
    compared to the nominal value, that'd cause the hangs.
    [driver.ino, integrated_revD.ino]
2025-10-24 New Mode: Scaled randomness
    Really helps at low push values, even if now we don't have the bug of
    nearly infinite waiting. Makes the pendulum noticably less energetic at
    low push values, exactly what we want.
    [driver.ino, integrated_revD.ino]
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2025-10-24 Fix 555 functionality; Cleanup wakup interrupt naming convention
    555 wake up function errantly also touched the pins for the 555 timer,
    putting the 555 timer into a wrong state.
    555 auto restarting is now tested to work; again.
    [555_restart.ino, driver.ino, integrated_revD.ino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]
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2025-10-26 Fix manual reset via UI; forgot a break.
    [integrated_revD.ino]
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2025-11-16 fix signs in software for the level shifter
    [driver.ino]
2025-11-19 Fix DAC calculation per datasheet.
    [DAC.ino]
2025-11-19 Fix debug modes (minorly)
    [driver.ino]
2025-11-20 Fix when DEBUG is false, for reasons I don't understand
    start_pendulum was hanging when #DEBUG was false.
    The hanging was coming from precise_idle. I have no idea why.
    Switching to more normal delays fixes it. Again, no idea why.
    [driver.ino]
2025-12-04 Begin AA battery life analysis from data tests from fluke 289
    flue is measuring the AA battery life.
    Man, we have lots of restarts. Not good.
    [Rev_D3_Amazon_AA.csv, Rev_D3_Energizer_Max_partial.csv]
2025-12-04 Fix pins for new rev
    [555_test.ino]
2025-12-04 Rework restart & Randomness so the pendulum starts more reliably
    Two innovations:
    1) pump extra energy into the pendulum near the time of the restart
    2) don't do the open-loop pushes as much, head straight to the better
    pushes.
    Also, increase the nominal push time... it honestly seems to help make
    the rev D3 pendulum more like rev C. I'm seeing high-energy limit cycle
    behaviour again.
    [constants.h, driver.ino]
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2025-12-05 Revert "Experimental Mode: Dynamically moving V2 for precise timing"
    This reverts commit 5cc0c5db58aae0a7fff29126ffcf6df5912cc9af.
    Per Issue tracker #22, this turned out to be not helpful
    [DAC.ino, constants.h, driver.ino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]
2025-12-06 Fix BEMF sensing to measure at a better time
    No o-scope, but on rev D with the op-amp that can keep up, it makes
    sense if we measure BEMF after the push we might have measured some
    flyback somwhere.
    Via prints, its tested to help massively in measuring more sensical
    speeds.
    [constants.h, driver.ino]
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2025-12-06 New feature: If Detect going too fast; skip several pushes and slow down
    [BEMF.ino, constants.h, driver.ino]
2025-12-06 Fix oversight: Errant restarting while skipping pushing
    [555_restart.ino, driver.ino]
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2025-12-12 battery test data
    The new system seems to be worse b/c it keeps on getting stuck. When it
    gets un-stuck, it needs serious power via the auto-restart function.
    This feels more mechanical than electrical.
    [Rev_C_Duracell.csv, Rev_C_Energizer_Max_partial.csv, Rev_D2_Duracell_first_mechanical.csv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]
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2025-12-14 Drive MOSFET at more optimum time, per issue tracker #22
    Will do better than this, but driving the MOSFET closer towards the peak
    BEMF really helps.
    [driver.ino, integrated_revD.ino]
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2025-12-15 Oops, fix a bad setting.
    [constants.h]
2025-12-15 Fix tests: Filename / 24:00:00 is invalid time (manually edit)
    [Rev_C_Duracell.csv, Rev_D3_Duracell_first_mechanical.csv]
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2025-12-19 MOre tests
    next step is the whisker-style plot to make it much easier to deduce if
    the reset happened in htat interval
    [Rev_D3_Energizer_Max_add_spacer_change_tunings.csv, Rev_D3_HDX_add_spacer_change_tunings.csv]
2025-12-28 Fix many erratta, overhaul power planes
    Rev D4 now WIP.
    [controller.brd, controller.sch]
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2026-01-02 Much analysis
    Can now detect reset pulses.
    Have some metrics to show how many times reset fires. Could use a few
    more.
    I think that the battery life right now is mostly constrained by how
    often the pendulum resets, which is a combo of;
    1) How many reset attempts it takes to successfully reset.
    2) How long (short) the pendulum goes between successive resets.
    I think we're burning most of the power resetting the pendulum.
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2026-04-05 Some pin renaming to make things easier to understand...
    [controller.brd, controller.sch]
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2026-04-07 New data: removing doublepushed significantly helped, but more required
    Still well below 100 hour performance of the rev C's.
    What's next:
    - Capacitor
    - Figure out some kind of better restart sequence (should I
    reverse-energize the magnet to pull in??)
    [Rev_D3_Enegizer_Prevent_Doublepush.csv]
2026-04-09 New data file & make parsing more reliable
    [Rev_D3_Duracel_Prevent_Doublepush.csv]
2026-04-22 New battery test
    Maybe not the most helpful one.
    [Rev_D4_Duracell_reset_eeprom_incomplete.test.csv]
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2026-04-25 (Mostly) fix debug prints
    some of hte power down modes break prints, some don't
    have to be careful with what I am using and when.
    [constants.h, driver.ino, integrated_revD.ino]
2026-04-25 datafile where the multimeter turned off
    Test conditions:
    Added the cap. HUGE difference.
    [Rev_D4_Duracell_reset_eeprom_test_contd.csv, question.csv]
2026-04-27 New test permutation - see Issue #25
    Big improvement by adding a cap!
    Probably likely on rev C that the big cap was doing a lot of heavy
    lifting...
    [Rev_D4_Duracel_Add_Cap.csv]
2026-05-05 Fix important timing calculation bug on reset extra push
    turns out I pushed more ... on the later pushes, not the earlier.
    And only calculated the new push value each Nth push, not each push.
    oops. Now it gets moving better if it did start moving.
    [driver.ino]
2026-05-05 Make restart better
    Rev D hardware doesn't need multiple pushes; just the first will do.
    Also remember to turn off the MOS when done.
    [driver.ino]
2026-05-05 Fix big oversight on starting
    Did not actually push extra (calculated hte extra push AFTER the push
    happened!)
    [driver.ino]
2026-05-24 another test with a big improvement
    Adding a giant 2200uf cap in the right place makes a big difference.
    https://github.com/dHutchings/double_pendulum/issues/25
    [Rev_D4_Duracel_Add_Cap_Change_Reset_A.csv, Rev_D4_Duracel_Add_Cap_Change_Reset_B.csv, Rev_D4_Duracel_Add_Cap_Change_Reset_C.csv]
2026-05-24 Some tests, but not sure what the test conditions were associated with them
    [Motor 20.csv, Motor 21.csv, Motor 22.csv]
2026-05-31 New data: over 6 days of operation
    Tested a smaller cap across the power leads. Unexepectedly, it did
    better than the larger.
    Plus it helps confuse USB chargers less.
    We now have verified data of at least 6 days operation - somewhere
    between 6 and 8 days of operation.
    [Rev_D4_Duracel_Add_2200uf_Cap.csv, Rev_D4_Duracel_Add_2200uf_Cap_Change_Reset_A.csv, Rev_D4_Duracel_Add_2200uf_Cap_Change_Reset_B.csv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]
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2026-06-07 Rev D5 - with cap - for the double pendulums
    Should be final rev.
    Was not able to export to 3d STEP model; Eagle STEP exporting might
    already be done. Eagle is being EOL'd.
    [controller.brd, controller.sch]
2026-06-14 spin a few different configs of spools
    For different 3d printers / tolerances. Some experimentation required.
    [Assem1.SLDASM, Pillar_assy.sldasm, custom_spool.SLDPRT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]
2026-06-22 Update plaque images
    Looks ok. maybe not perfect, but ok Maybe a little crowded.
    [controller_d5_san.DXF, controller_d5_san.SLDDRW, plaque_image.SLDDRW]

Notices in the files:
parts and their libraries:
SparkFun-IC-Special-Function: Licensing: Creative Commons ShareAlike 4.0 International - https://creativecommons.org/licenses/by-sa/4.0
